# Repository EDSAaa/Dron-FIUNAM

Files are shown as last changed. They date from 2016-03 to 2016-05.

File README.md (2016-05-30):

## Dron-FIUNAM ##

This is a repository that contains the source code of a project developed at UNAM in Mexico, which was a thesis for obtain a degree. 

The purpose of the project was the design, construction and control of an aerial vehicle kind of dron, which could be a system for a laboratory of Automatic Control. At the beginning, the team couldn't decide between the different sort of existing vehicles, but finally was chosen a quadcopter in *X* configuration.

The dron has the components that are listed below:

- Flight Controller (FC) All In One Pro V.2
- Teensy V3.1
- (4) Gemfan 5x4 propellers
- (4) Baby Beast 2150 [KV] Brushless Motors
- (4) X Afro ESC 12 [A]
- LiPo Battery Turnigy Nanotech 3S 45~90C 1300 [mAh]
- 3D printed frame class 250

The operation of the quadcopter is as follows. On the one hand, The FC was programmed with a release of MultiWii, only for use it like a Data Acquisition Module. And on the other hand Teensy has implemented the MultiWii Serial Protocol (MSP) to request all the sensor data to the FC. Simultaneously, this microcontroller calculates a State Feedback Controller and sends the PWM signals to the brushless motors.

The State Feedback controller only consider 8 states (which can be measured with the FC): *z*, *roll*, *pitch*, *yaw*, and its derivatives with respect to time. Thats why the controller only can only adjust the height, but not the *xy* position.
 
This repository includes both the programs that were made for obtain the mathematical model and those that were made for controlling the quadcopter.

### LabVIEW ###

This folder contains the interface that allows the operator manipulate the desired *z*, and watch the graphics of the system variables behavior.

### Mathematica ###

This folder has the file that calculates the mathematical modelling of a quadcopter in *X* configuration using Euler - Lagrange Equations. This includes the Equations of Motion and the State Space Model in their nonlinear form, and also includes the Linear State Space Model.

Because all the model was obtained symbolically, you can use this program to obtain a model for any *X* quadcopter, only changing the numeric values with the parameters of your device.

### Matlab ###

There are some files.

- One is a .m script that contains the numeric parameters of the dron. In this file was designed a LQR Controller.
- Other is a Simulink file, which has the necessary blocks for simulating the response of the system (model linear and non linear) with  the controller implemented.
- There is a file that simulates the effects noise in the mesure of z.

### Teensy v3.1 ###

Here are one program written in Wiring (C for Arduino). 

The program contains the implementation of MultiWii Serial Protocol, whose purpose is allow Tensy request the values of the sensors to the Flight Controller. And with those vales it calculates a State Feedback Controller.

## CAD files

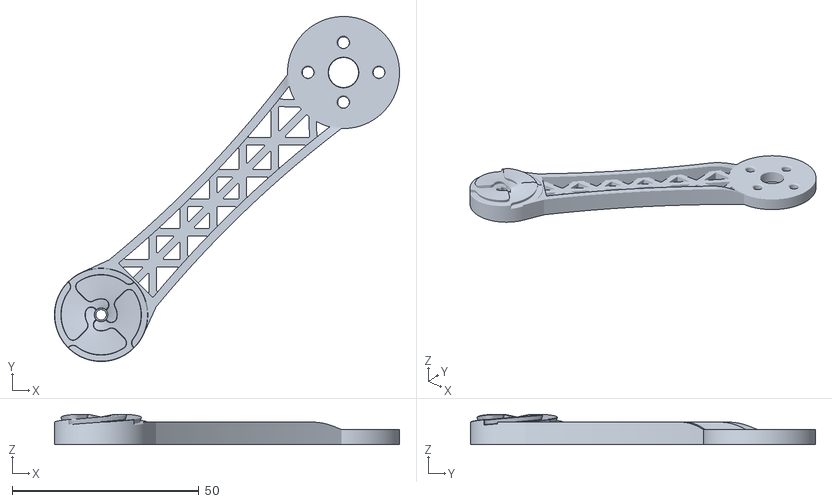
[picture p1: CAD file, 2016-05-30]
STL/BrazoRotite.stl
92.4 x 92.4 x 8.07

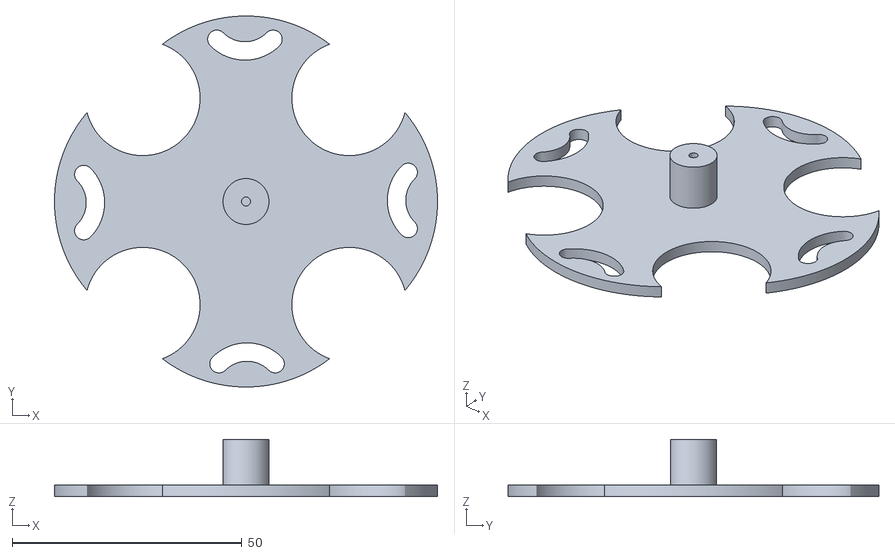
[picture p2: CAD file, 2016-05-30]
STL/PlacaBase.stl
83.4 x 80.8 x 12.5

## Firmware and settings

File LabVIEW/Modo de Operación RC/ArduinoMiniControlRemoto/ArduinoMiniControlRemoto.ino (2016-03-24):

//Programa para probar el dron como RC

#include <stdlib.h> 
#include <Servo.h> 

#define PINTHROTTLE 2  
#define PINROLL 3
#define PINPITCH 4
#define PINYAW 5
#define PINAUX1 6
#define PINAUX2 7
#define MAXIMOPWM 2000   
#define MINIMOPWM 1000    
#define  BAUD 57600   
  
Servo Throttle;
Servo Roll;
Servo Pitch;
Servo Yaw;
Servo CanalAux1;
Servo CanalAux2;

int throttle=0;
int roll=0;
int pitch=0;
int yaw=0;
int aux1=0;
int aux2=0;
int tiempoCiclo=10;
int timeWithoutConection=0;

int LeerDato(void);  //Prototipo de la función LeerDato
void PararMotores(void); //Prototipo de la función PararMotores

void setup() 
{
  
  Serial.begin(BAUD);
  Throttle.attach(PINTHROTTLE); 
  Roll.attach(PINROLL);
  Pitch.attach(PINPITCH);
  Yaw.attach(PINYAW);
  CanalAux1.attach(PINAUX1);
  CanalAux2.attach(PINAUX2);
  
  delay(500);
  
}

void loop() 
{

  if(Serial.available()>=24)
  {
    
    throttle = LeerDato();
    roll = LeerDato();
    pitch = LeerDato();
    yaw = LeerDato();
    aux1=LeerDato();
    aux2=LeerDato();

     
    Throttle.writeMicroseconds(throttle);
    Roll.writeMicroseconds(roll);
    Pitch.writeMicroseconds(pitch);
    Yaw.writeMicroseconds(yaw);
    CanalAux1.writeMicroseconds(aux1);
    CanalAux2.writeMicroseconds(aux2);

    
    timeWithoutConection=0;
  }
  else
  {
    Serial.write("Crap");
    timeWithoutConection+=tiempoCiclo; //Si no se recibió ningún dato, incrementa el tiempo sin conexión
  }
  
  //Por seguridad, si no se reciben datos en 1 segundos, se decrementa la velocidad hasta apagar los motores
 
  if(timeWithoutConection>=1000)
  {
    PararMotores();
  }


  delay(tiempoCiclo);
  
}

//Función LeerDato
int LeerDato(void)
{
  
  String cadena="";
  char auxiliar;
  
  for(int i=0;i<4;i++)
  {
      auxiliar=(char)Serial.read();
      cadena+=auxiliar;
  }
  
  for(int i=0;i<4;i++)
  {
    Serial.write(cadena[i]);
  }
  return cadena.toInt();
    
}//Fin de la función LeerDato



//Función PararMotores
void PararMotores(void)
{
  while(throttle>1100)
  {
    throttle-=50;
    Throttle.writeMicroseconds(throttle);
   
    delay(50);
  }
  
  throttle=1000;  
  Throttle.writeMicroseconds(throttle);
  
}

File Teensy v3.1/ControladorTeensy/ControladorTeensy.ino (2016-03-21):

//Cabecera del controlador
#include "Controlador.h"

//Cabecera del protocolo de comunicación
#include "protocol.h"

//Máquina de estados
#ifndef serialstate_h
#define serialstate_h
#include "serialstate.h"
#endif



#define Ts 20
#define INBUF_SIZE 64
#define  BAUD 57600   

//Variables para la máquina de estados
static uint8_t inBuf[INBUF_SIZE];
static uint8_t checksum;
static uint8_t commandMW;
static uint8_t offset;
static uint8_t dataSize;

static Protocol p;

int8_t c,n;  

//Tiempos inicial y final
int ti=0;
int tf=0;

int aux=0;
float zRef=0;

XYAngle angles;
Altitude alt;
IMUValues imu;

void setup()  
{
  pinMode(led,OUTPUT);
  Serial2.begin(BAUD);  //telemetría
  Serial1.begin(BAUD); //Multiwii

  Mot1.attach(PINMOTOR1);
  Mot2.attach(PINMOTOR2);
  Mot3.attach(PINMOTOR3);
  Mot4.attach(PINMOTOR4);
  
  escCalibration();
  delay(1000);
  inicialization();
  //Serial2.write((byte *)"Ya calibre",10);
  startMotors();
  delay(2000);
}

void loop() // run over and over
{

  ti=millis();
 
  if(aux==255)
  {
    emergencyStop();
    inicialization();
    startMotors();
    delay(2000);
  }
  else 
  {
    if(Serial2.available()>0)
    {
      aux = Serial2.read();
    }
    
    uint8_t  datad = 0;
    uint8_t  *data = & datad;
    p.send_msp( MSP_ATTITUDE  ,data, 0);
    readData();
    p.send_msp( MSP_ALTITUDE  ,data, 0);
    readData();
    p.send_msp( MSP_RAW_IMU  ,data, 0);
    readData();
    zRef=(float)(aux/100.00);  
    control(zRef,angles.angleX,angles.angleY,angles.heading,alt.value,alt.vel,imu.gyroX,imu.gyroY,imu.gyroZ);
    aux=0;
    tf=millis();
    delay(Ts-(tf-ti));
  }
  
}

void readData() {

  delayMicroseconds(3000);
 

  while (Serial1.available()) {

    byte c = Serial1.read();
    Serial2.write(c);

    if (c_state == IDLE) {
      c_state = (c=='$') ? HEADER_START : IDLE;
    } 
    else if (c_state == HEADER_START) {
      c_state = (c=='M') ? HEADER_M : IDLE;
    } 
    else if (c_state == HEADER_M) {
      c_state = (c=='>') ? HEADER_ARROW : IDLE;
    } 
    else if (c_state == HEADER_ARROW) {

      if (c > INBUF_SIZE) {  // now we are expecting the payload size
        c_state = IDLE;

      } 
      else {
        dataSize = c;
        offset = 0;
        checksum = 0;
        checksum ^= c;
        c_state = HEADER_SIZE;  
      }
    } 
    else if (c_state == HEADER_SIZE) {
      commandMW = c;
      checksum ^= c;
      c_state = HEADER_CMD;
    } 
    else if (c_state == HEADER_CMD && offset < dataSize) {
      checksum ^= c;
      inBuf[offset++] = c;
    } 
    else if (c_state == HEADER_CMD && offset >= dataSize) {

      if (checksum == c) {
        if (commandMW == MSP_ATTITUDE) {
          angles = p.evalAtt(inBuf);
          //Serial.print("Ang x: " + (String)(float)(result.angleX/10.0) + "\tAng y: " + (String)(float)(result.angleY/10.0) + "\tAng z: " + (String)(float)result.heading);
          //Serial2.write(result.angleX);
          //Serial2.write(result.angleY);
          //Serial2.write(result.heading);

          
        }
        if (commandMW == MSP_ALTITUDE) {
          alt = p.evalAlt(inBuf);
          //Serial.print("\tAlt: "+(String)(float)(result.value/100.0)+"\tVelZ: "+(String)(float)(result.vel));
          
        }
        if (commandMW == MSP_RAW_IMU) {
          imu = p.evalIMU(inBuf);
           //Serial.println("\tVelAngX: "+(String)(float)(result.gyroX/4.096*pi/180)+"\tVelAngY: "+(String)(float)(result.gyroY/4.096*pi/180 )+"\tVelAngZ: "+(String)(float)(result.gyroZ/4.096*pi/180 ));
          
        }
        
      } 

      c_state = IDLE;
    }

  }
}

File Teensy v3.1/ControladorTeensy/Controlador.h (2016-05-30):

#include <Arduino.h>

//Accionar motores
#include <Servo.h>

//Constantes para los motores
#define MAXPWM 1900 
#define MINESC 1000  
#define MINPWM 1350
#define PINMOTOR1 2  
#define PINMOTOR2 3
#define PINMOTOR3 4
#define PINMOTOR4 5  
#define pi 3.141592
#define OMEGAEQ 1211.85

//Objetos de la clase Servo para los motores
Servo Mot1;
Servo Mot2;
Servo Mot3;
Servo Mot4;

int inicializationAux=0;

//Variables para el controlador
float angx = 0;
float angy = 0;
float angz = 0;
float z = 0;
float velz = 0;
float gyrox = 0;
float gyroy = 0;
float gyroz = 0;
float omega1 = 0; 
float omega2 = 0; 
float omega3 = 0; 
float omega4 = 0;
int pwmM1=0;
int pwmM2=0;
int pwmM3=0;
int pwmM4=0;

//Variables para generar gráficas
float ANGULOX=0;
float ANGULOY=0;
float ANGULOZ=0;

void escCalibration(void)
{
  Mot1.writeMicroseconds(MAXPWM);
  Mot2.writeMicroseconds(MAXPWM);
  Mot3.writeMicroseconds(MAXPWM);
  Mot4.writeMicroseconds(MAXPWM);
  delay(3000);
  Mot1.writeMicroseconds(MINESC);
  Mot2.writeMicroseconds(MINESC);
  Mot3.writeMicroseconds(MINESC);
  Mot4.writeMicroseconds(MINESC);
  delay(2000);
}

void startMotors(void)
{
  //Se arrancan paulatinamente los motores
  for(int i=MINESC;i<=MINPWM;i=i+10)
  {
    Mot1.writeMicroseconds(i);
    Mot2.writeMicroseconds(i);
    Mot3.writeMicroseconds(i);
    Mot4.writeMicroseconds(i);
    delay(30);
  }
  
  Serial2.write((byte *)"Arranqué",8);
}

void emergencyStop(void)
{     
  Mot1.writeMicroseconds(MINESC);
  Mot2.writeMicroseconds(MINESC);
  Mot3.writeMicroseconds(MINESC);
  Mot4.writeMicroseconds(MINESC);
  delay(1000);
}


void control(float zr, int16_t ax, int16_t ay, int16_t az, int16_t al, int16_t vz, int16_t gx, int16_t gy, int16_t gz)
{
  
  //Ángulos para el controlador en radianes
  angx = ax/10.0*pi/180;
  angy = -ay/10.0*pi/180;
  angz = -az*pi/180;

  
  z = al/100.0; //Altura en m
  velz = vz/100.0;  //Velocidad en m/s
  
  //Velocidades angulares en rad/s
  gyrox = gx/4.096*pi/180;
  gyroy = -gy/4.096*pi/180; 
  gyroz = -gz/4.096*pi/180;

  //ECUACIONES DEL CONTROLADOR (Cálculo de las omegas del sistema trasladado al punto de equilibrio)
  omega1 = 91.14*angx - 91.27*angy + 14.3*angz + 46.14*gyrox - 46.25*gyroy + 46.78*gyroz - 92.35*velz - 49.25*(z-zr);
  omega2 = - 91.14*angx - 91.27*angy - 14.3*angz - 46.14*gyrox - 46.25*gyroy - 46.78*gyroz - 92.35*velz - 49.25*(z-zr);
  omega3 = 91.27*angy - 91.14*angx + 14.3*angz - 46.14*gyrox + 46.25*gyroy + 46.78*gyroz - 92.35*velz - 49.25*(z-zr);
  omega4 = 91.14*angx + 91.27*angy - 14.3*angz + 46.14*gyrox + 46.25*gyroy - 46.78*gyroz - 92.35*velz - 49.25*(z-zr);

  //Cálculo de las omegas del sistema
  omega1 += OMEGAEQ;
  omega2 += OMEGAEQ;
  omega3 += OMEGAEQ;
  omega4 += OMEGAEQ;

  //Cálculo de los tiempos en alto para cada motor
  pwmM1 = constrain((int)((0.0002730)*omega1*omega1 + 1004), MINPWM, MAXPWM);
  pwmM2 = constrain((int)((0.0002730)*omega2*omega2 + 1004), MINPWM, MAXPWM);
  pwmM3 = constrain((int)((0.0002730)*omega3*omega3 + 1004), MINPWM, MAXPWM);
  pwmM4 = constrain((int)((0.0002730)*omega4*omega4 + 1004), MINPWM, MAXPWM);

  //Impresiones en pantalla para generar las gráficas
  //Serial.println("Motor1: " + (String)pwmM1 + "\tMotor2: " + (String)pwmM2 + "\tMotor3: " + (String)pwmM3 + "\tMotor4: " + (String)pwmM4 + "\tzref: " + (String)zr + "\tz: " + (String)z);
  //Serial.println("Motor1:*"+(String)pwmM1+"*Motor2:*"+(String)pwmM2+"*Motor3:*"+(String)pwmM3+"*Motor4:*"+(String)pwmM4+"*X*"+(String)ANGULOX+"*Y*"+(String)ANGULOY+"*Z*"+(String)ANGULOZ);

  //Se envían las señales a cada ESC, y consecuentemente a cada motor
  Mot1.writeMicroseconds(pwmM1);
  Mot2.writeMicroseconds(pwmM2);
  Mot3.writeMicroseconds(pwmM3);
  Mot4.writeMicroseconds(pwmM4);
}

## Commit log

2016-03-21 Actualización de Archivos
    Primera actualización de archivos en el repositorio.
2016-03-21 Teensy
    Actualización del Controlador
2016-04-18 Actualización de programas
